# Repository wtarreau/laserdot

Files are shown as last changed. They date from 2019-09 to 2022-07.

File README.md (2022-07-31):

laserdot
========

A small program running in a microcontroller to place between a laser engraver
controller and the laser module to always turn the laser on at a very low duty
cycle, permitting to see the dot to adjust the focus, position and alignment.

Just build it using "make MCU=" with the microcontroller name (attiny85 and
attiny13 are currently supported, others may be trivially added).

It has no dependency beyond an AVR toolchain like the one provided with any
Arduino IDE. The program can also trivially be imported as an Arduino project
for those more familiar with this heavier approach.

A circuit is provided, made of a schematic and a board, for those who want to
quickly implement it. It's made around an ATTINY13A which is as cheap as a
555 these days. The output uses 4 pins at 2.0 pitch to match my NEJE-20W laser
module, and the input uses a male JST-XH 2.54mm connector to match the
connector at the end of the cable on the laser module side. It's worth noting
that the cable is not straight but reversed, so the polarity here really
requires the cable or needs to be reversed.

The micro-controller may be programmed in situ using an SOP8 clamp provided
the module is disconnected from both sides. Indeed, no pin prevents this from
being done since there are no local component connections. I'm also using this
to program a different duty cycle in its EEPROM, like here, 0.2% duty cycle :

```
$ avrdude -c buspirate -P /dev/ttyUSB0 -p attiny13 -U eeprom:w:0x02:m
```

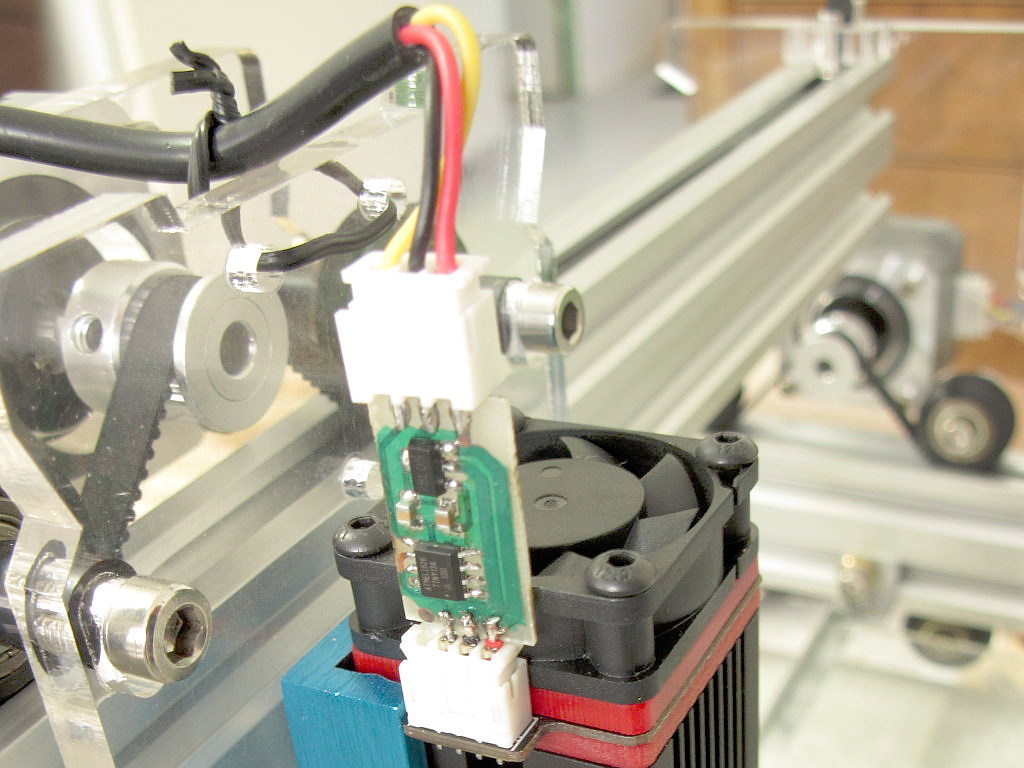
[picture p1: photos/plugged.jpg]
The module connected to a laser module


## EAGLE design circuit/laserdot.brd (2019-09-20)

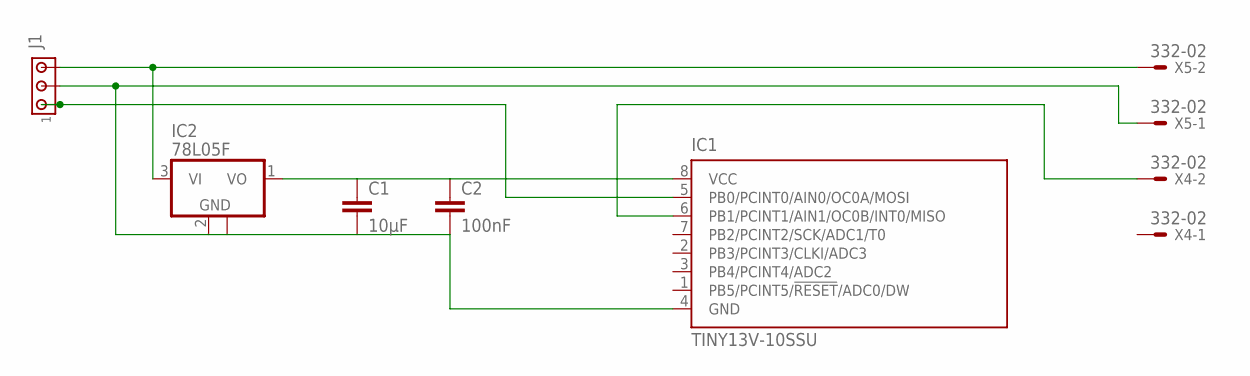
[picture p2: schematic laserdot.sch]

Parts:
C1: 10µF; C0805
C2: 100nF; C0805
IC1: TINY13V-10SSU; 8S1
IC2: 78L05F; SOT89
J1: MTA03-100; 10X03MTA
X4, X5: 332-02

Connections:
unnamed: IC2.3 (VI), J1.3, X5.2
unnamed: C1.2, C2.2, IC1.4 (GND), IC2.2 (GND), IC2.2@1 (GND), J1.2, X5.1
unnamed: IC1.5 (PB0/PCINT0/AIN0/OC0A/MOSI), J1.1
unnamed: C1.1, C2.1, IC1.8 (VCC), IC2.1 (VO)
unnamed: IC1.6 (PB1/PCINT1/AIN1/OC0B/INT0/MISO), X4.2

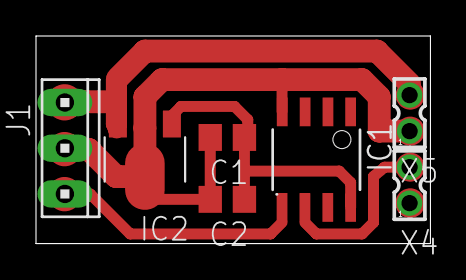
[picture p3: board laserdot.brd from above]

Board: 2 copper layers, 21.9 x 11.5 mm, 7 parts (0 on the bottom side), 5 nets.

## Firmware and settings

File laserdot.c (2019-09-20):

/* laserdot.c - 2019/09/16 - Willy Tarreau - public domain
 *
 * This is a C AVR implementation of a PWM minimum value to control a laser
 * module. The idea is that on laser engravers it's mandatory to see the dot
 * to adjust the axis, and some modules do not provide a button to enable the
 * laser. Since the laser at very low power is harmless to whatever surface it
 * is sent to, this simply makes sure that a minimum duty cycle is always
 * enforced when the PWM is off for too long.
 *
 * The principle is to wait for a pulse for no more than 2 milliseconds. If it
 * does not happen in two milliseconds then a short pulse is sent to turn the
 * beam on. The pulse length is configured in the eeprom at address 0, as a
 * thousands of a period, thus with a maximum of 25% duty cycle. Value 0xFF is
 * considered unset and is replaced by the default value, 0x05 (0.5%). The
 * code is small enough to be flashed next to a Digispark's boot loader. It
 * can also be ported to an ATTINY13A (without boot loader though).
 *
 * The code is written in Arduino style using setup() and loop() so that it is
 * easily ported to other environments. But it has no external dependency.
 */

/* Internal frequency, 16 MHz for T25/45/85, 9.6 MHz for T13 */
#ifndef F_CPU
#error "Must set F_CPU to the CPU's frequency in Hz"
#endif

#include <avr/io.h>
#include <avr/eeprom.h>
#include <stdint.h>

/* intensity value for the pulse length in microseconds per millisecond, stored
 * in the EEPROM. Thus it corresponds to the duty cycle in thousands. Write it
 * using avrdude with "-U eeprom:w:" $value ":m". Example with 0x0A :
 *    $ avrdude ... -U eeprom:w:0x0a:m
 */
static const uint8_t intensity EEMEM;
static uint16_t pulse_high; // pulse width in cycles, high state
static uint16_t pulse_low;  // pulse width in cycles, low state

/* max loops with the signal not changing, that's about 1.25 milliseconds
 * at 16 MHz and 2 ms at 9.6 MHz.
 */
#define STUCK 4000

/* Convert microseconds to loops around an empty asm statement. Each loop was
 * measured to take 5 cycles on gcc 5.4 (vs 4 on 4.3)! This is limited to 64k
 * loops, or ~20ms at 8 MHz, 17ms at 9.6 MHz.
 */
static inline uint16_t us2loops(uint16_t us)
{
	return (uint32_t)us * (F_CPU / 100000) / 50 + 1;
}

/* Sleeps this number of cycles. Limited ~32ms at 8 MHz, 27ms at 9.6 MHz. */
static inline void delay(uint16_t loops)
{
	while (loops--)
		asm volatile("");
}

/* send a positive pulse of <width> cycles on port B<port> */
static inline void send_pulse(uint8_t port, uint16_t width)
{
	PORTB |= _BV(port);
	while (width--)
		asm volatile("");
	PORTB &= ~_BV(port);
}

/* Sleeps this number of microseconds. Limited ~32ms at 8 MHz, 27ms
 * at 9.6 MHz. May overflow on 8 MHz CPUs above 8 milliseconds at once.
 */
static inline void delay_us(uint16_t us)
{
	delay(us2loops(us));
}

/* send a positive pulse of <width> microseconds on port B<port> */
static inline void send_pulse_us(uint8_t port, uint16_t width)
{
	send_pulse(port, us2loops(width));
}

/* The loop is pretty simple. We wait for the input to change or a timeout to
 * appear. If the timeout strikes, we send a short pulse of <pulse> width in a
 * period of 1 ms. Otherwise we simply copy the signal and wait for the next
 * change. This way it covers disconnected inputs and zero as well.
 */
void loop(void)
{
	uint16_t tout;

	while (1) {
		tout = STUCK;
		while (!(PINB & _BV(PB0))) {
			if (__builtin_expect(!tout--, 0)) {
				send_pulse(PB1, pulse_high);
				delay(pulse_low);
				tout = STUCK;
			}
		}
		/* the pulse started */
		PORTB |= _BV(PB1);

		tout = STUCK;
		while (PINB & _BV(PB0)) {
#ifdef LIMIT_PULSE_UP
			if (__builtin_expect(!tout--, 0)) {
				send_pulse(PB1, pulse_high);
				delay(pulse_low);
				tout = STUCK;
			}
#endif
		}
		/* the pulse stopped */
		PORTB &= ~_BV(PB1);
	}
}

void setup(void)
{
	/* PB#  pin  dir  role
	 * PB0   5    in  PWM in
	 * PB1   6   out  PWM out
	 * PB2   7    -   unused
	 * PB3   2    -   unused
	 * PB4   3    -   unused
	 * PB5   1    -   RESET
	 */

	/* set output pins */
	DDRB = _BV(DDB1);

	/* enable pull-up on PB0 */
	PORTB |= _BV(PB0);

	/* stop pulse output on PB1 */
	PORTB &= ~_BV(PB1);

	pulse_high = eeprom_read_byte(&intensity);
	if (pulse_high == 0xff)
		pulse_high = 5; // 0.5% by default
	pulse_low  = us2loops(1000 - pulse_high);
	pulse_high = us2loops(pulse_high);
}

int main(void)
{
	setup();
#if TEST
	/* must produce exactly 1 KHz signal on PB1 */
	while (1) {
		delay_us(500);
		PORTB ^= _BV(PB1);
	}
#else
	while (1)
		loop();
#endif
}

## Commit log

2019-09-20 code: create the first working version of the program
    The program retrieves the minimum duty cycle to use from the first
    eeprom's address and falls back to 0.5% if unset. It supports the
    TINY versions of AVR devices, with input on PB0 and output on PB1.
    It simply copies the input to the output and sends small pulses
    when the input is idle for too long. With high a enough clock it
    doesn't introduce any measurable latency effect, as the signal
    will typically be shifted by less than 10 cycles. Getting out of
    idle may take up to one millisecond if the input signal arrives at
    the beginning of the pulse, but even one millisecond corresponds
    to only 20 microns at an engraving speed of 1200mm/min so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
    [laserdot.c]
2019-09-20 build: add a Makefile
    It supports attiny85 and attiny13 (to be set using MCU=) and can
    directly flash the device (make upload). The programmer defaults
    to a bus pirate, but it can also work with other ones like usbasp
    or usbtiny if needed.
2019-09-20 circuit: add the laserdot schematic and board
    These ones are really trivial since there are only 4 components but they can
    save time to those willing to reimplement the circuit. The output uses 4 pin
    at 2.0 pitch to match my NEJE-20W laser, and the input uses a male JST-XH
    2.54mm connector to match the connector at the end of the cable on the laser
    module side. It's worth noting that the cable is not straight but reversed,
    so the polarity here really requires the cable or needs to be reversed.
    [laserdot.brd, laserdot.sch]
